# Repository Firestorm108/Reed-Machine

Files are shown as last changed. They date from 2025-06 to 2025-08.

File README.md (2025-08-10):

# Reed-Machine
Ever opened a new reed but it just felt stiff? That's the purpose of the Reed Machine; to speed up the break-in process so you can swap reeds quickly as well as get current reeds in better shape. The Reed Machine will send various types of energy throughout the reed to break it in faster. Sometimes, my current reed breaks at the wrong times and having a little machine that prepares my next reed for me just sitting in my case would be great.

Demo: https://www.youtube.com/shorts/aRf1Y5GJrq0


CleanShot 2025-06-19 at 00 02 53

CleanShot 2025-06-15 at 17 43 31

CleanShot 2025-07-17 at 19 17 57

CleanShot 2025-06-19 at 00 05 56

CleanShot 2025-06-19 at 00 05 45

CleanShot 2025-06-18 at 23 51 14

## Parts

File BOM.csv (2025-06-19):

1KG PETG- $0
Rubber Feet- $6.99 (https://www.amazon.com/Bumpers-Adhesive-Cabinets-Picture-Dampening/dp/B07PWCC6KP)
Small Vibration Motors- $5 (https://www.aliexpress.us/item/3256807967305634.html)
Medium Vibration Motors- $10 (https://www.amazon.com/Vibration-Waterproof-8000-20000RPM-Electronic-equipments/dp/B0CY2KLH2P/) (From amazon due to no reputable supplier of the desired product on Aliexpress)
12V Silicone Heating Element (2)- $6 (https://www.aliexpress.us/item/3256805550724269.html)
5V BLDC Fan- $2.42 (https://www.aliexpress.us/item/3256804645826698.html) (4015 Model)
Thermistor Probe- $3 (https://www.aliexpress.us/item/3256807802845094.html)
IRLZ44N MOSFETS- $7.73 (https://www.aliexpress.us/item/3256806042313742.html)
DHT22- $2.24 (https://www.aliexpress.us/item/3256806161971824.html)
Arduino Nano- $3.54 (https://www.aliexpress.us/item/3256806286441000.html)
OLED Screen- $2.26 (https://www.aliexpress.us/item/3256805954920554.html)
RGB LEDs- $4.81 (https://www.aliexpress.us/item/2251832091998418.html)
Rotary Encoder $3.64 (https://www.aliexpress.us/item/2261799870168498.html)
18650 Cells + Shipping (2) $14.84 (https://batteryhookup.com/collections/frontpage/products/new-eve-icr18650-26v-3-6v-2550mah-18650-li-ion-cells)
5v Boost Converter $2.49 (https://www.aliexpress.us/item/2251832713406135.html)
Charging Board USB-C $3 (https://www.aliexpress.us/item/3256806796332131.html)
PCB: $32.62 (w/ cheapest shipping option)
18650 Cell Holders $3 (https://www.aliexpress.us/item/3256804898031489.html)
Screws $15 (https://www.amazon.com/Assortment-Machine-Washers-Phillips-Slotted/dp/B0BN297MP5/)
Total Cost $123.07

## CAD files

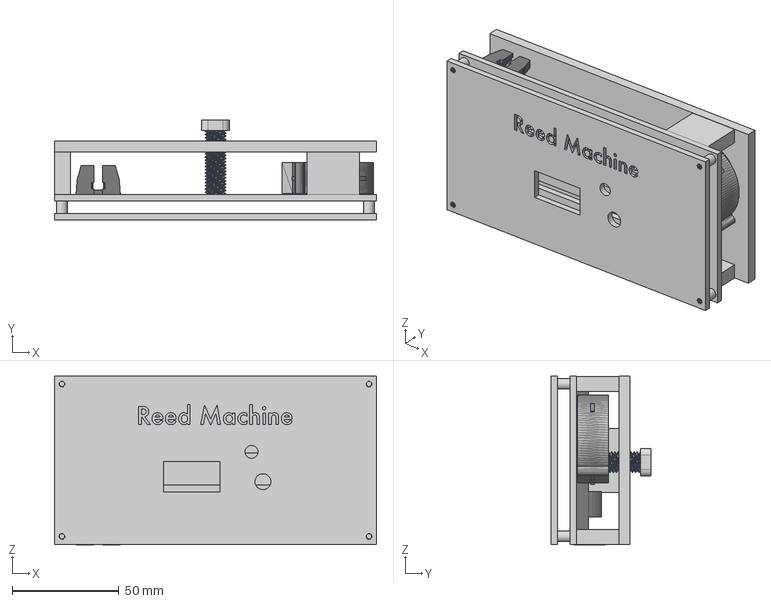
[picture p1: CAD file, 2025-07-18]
CAD_files/Reed Machine Case v25.step
151.0 x 47.0 x 79.1 mm
Fan 97
Battery Holder

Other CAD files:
CAD_files/Reed Machine Case v25.f3z
CAD_files/Reed Machine Case v25.stl

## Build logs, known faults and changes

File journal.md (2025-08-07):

Total Time Spent: 17 Hours

June 14th-
I spent some time researching parts, and thought about my idea. I just came up with a rough idea today overall to guide and think upon. I also completed the BOM just now. As well as the PCB layout. I will route it tomorrow.

June14

CleanShot 2025-06-14 at 23 08 13

Time Spent: ~4 Hours

June 15-

Today, I changed around the components a bit (ESP32 -> Arduino Nano) and got rid of the switch due to the rotary encoder having one built in. I did the routing for the PCB which took wayyy longer than expected especially with the footprints not working properly so I had like 15 errors. I had to manually edit the footprints but luckily it works now. I also completed the wiring diagram. After that, I designed the entire casing where I learned a lot of new things. I really like how the case came out, and I think it'll look cool. I think it needs some polishing to look a little cleaner which I will make sure to do. CleanShot 2025-06-15 at 17 11 57
I had a lot of trouble with routing especially but I'm super proud of this PCB and hope it works.
CleanS![CleanShot 2025-06-15 at 22 40 53](https://github.com/user-attachments/assets/ecce8b8f-1308-4cad-9ebe-20b63bdc63df) hot 2025-06-15 at 17 44 24
The wiring diagram is pretty basic since mostly everything is on the PCB.

CleanShot 2025-06-15 at 22 42 03

The casing is pretty cool, there's a clamp on the top to hold the reed down, space in the front for the OLED, rotary encoder, and LED. In the back, there are vents for airflow and housing for the components with a sliding door to put the reed in.

Time Spent: ~12 Hours

June 16-

Polished up the 3d files, BOM, and other files to get it ready to submit. (Nothing large, just making sure everything is in the right place)

Time Spent: ~1 Hour

July 9-

I left all the parts to print overnight today. Tomorrow the goal is to speedrun building the entire project to bring to undercity.

Time Spent: ~1 Hour

July 17th

I printed all my files, and nothing fit lol. 

Nothing, not the batteries, not the PCB, not the thumbscrew.

Absolutely nothing!

So I completely redesigned the entire case and now it's much thinner and better overall.

CleanShot 2025-07-17 at 19 02 57

CleanShot 2025-07-17 at 19 02 48

<h1>August 7th</h1>

Today I built the whole thing! Numerous things went wrong, it was horrible. First, the original microcontroller came broken. I tried to use an ESP32. But I needed 5V logic. So, I had to go with a random barely working arduino, my first ever. I'm glad that I had it though otherwise this project wouldn't have been possible. 
This first picture is me earlier today when I was wiring and everything was nice and happy in the world.


Then, disaster struck! My 18650 cell shorted itself and the wire insulation started dripping. I remember feeling a burn on my arm, looking back, seeing smoke coming out, and then cutting the wires immediately cause I was scared lol.
It's okay though it all works now.



I watched over 30 episodes of Brooklyn 99 working on this I believe (this picture was taken at 3am), it was a fun time though, chilling, working on the project.



Finally I just finished the project. I tested it out on my saxophone, and it actually works pretty well! My tone is noticeably better and I can hit lower notes way easier.



Total Time Spent: 12 Hours

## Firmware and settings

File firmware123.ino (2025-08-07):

#include <Wire.h>
#include <Adafruit_GFX.h>
#include <Adafruit_SSD1306.h>
#define SCREEN_WIDTH 128
#define SCREEN_HEIGHT 64
#define OLED_RESET    -1
Adafruit_SSD1306 display(SCREEN_WIDTH, SCREEN_HEIGHT, &Wire, OLED_RESET);
const int rotaryClkPin = 11;
const int rotaryDtPin = 12;
const int buttonPin = 13;
const int mosfetPins[] = {8, 9, 10};
int lastClkState;
int menuIndex = 0;
unsigned long durations[] = {60000, 120000, 180000};  // in ms
String labels[] = {"60s", "120s", "180s"};
bool selectionMade = false;
unsigned long startTime = 0;
void setup() {
  pinMode(rotaryClkPin, INPUT_PULLUP);
  pinMode(rotaryDtPin, INPUT_PULLUP);
  pinMode(buttonPin, INPUT_PULLUP);

  for (int i = 0; i < 3; i++) {
    pinMode(mosfetPins[i], OUTPUT);
    digitalWrite(mosfetPins[i], LOW);
  }

  lastClkState = digitalRead(rotaryClkPin);

  Serial.begin(9600);

  if (!display.begin(SSD1306_SWITCHCAPVCC, 0x3C)) {
    Serial.println(F("OLED not found"));
    while (true);
  }

  displayMenu();
}
void loop() {
  if (!selectionMade) {
    int clkState = digitalRead(rotaryClkPin);
    int dtState = digitalRead(rotaryDtPin);

    if (clkState != lastClkState && clkState == LOW) {
      if (dtState != clkState) {
        menuIndex++;
      } else {
        menuIndex--;
      }

      if (menuIndex < 0) menuIndex = 2;
      if (menuIndex > 2) menuIndex = 0;

      displayMenu();
    }

    lastClkState = clkState;

    if (digitalRead(buttonPin) == LOW) {
      delay(200); 
      if (digitalRead(buttonPin) == LOW) {
        startTime = millis();
        selectionMade = true;

        for (int i = 0; i < 3; i++) {
          digitalWrite(mosfetPins[i], HIGH);
        }

        display.clearDisplay();
        display.setTextSize(2);
        display.setTextColor(SSD1306_WHITE);
        display.setCursor(0, 20);
        display.print("Running: ");
        display.print(labels[menuIndex]);
        display.display();
      }
    }
  } else {
    if (millis() - startTime >= durations[menuIndex]) {
      selectionMade = false;

      for (int i = 0; i < 3; i++) {
        digitalWrite(mosfetPins[i], LOW);
      }

      displayMenu();
    }
  }
}
void displayMenu() {
  display.clearDisplay();
  display.setTextSize(2);
  display.setTextColor(SSD1306_WHITE);
  display.setCursor(0, 0);
  display.println("Select Time:");
  display.setCursor(0, 25);
  display.print(">");
  display.println(labels[menuIndex]);
  display.display();
}

                
